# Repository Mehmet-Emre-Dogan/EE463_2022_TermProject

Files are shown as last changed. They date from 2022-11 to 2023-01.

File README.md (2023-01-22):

# EE463 2022 Term Project
2 kW Smart DC motor drive.
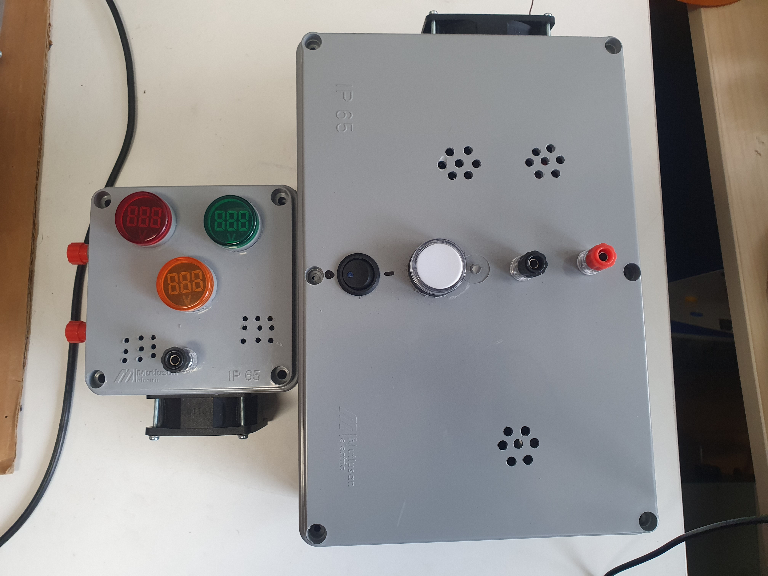
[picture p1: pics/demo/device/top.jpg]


# Circuit Diagrams

## Main Block Diagram
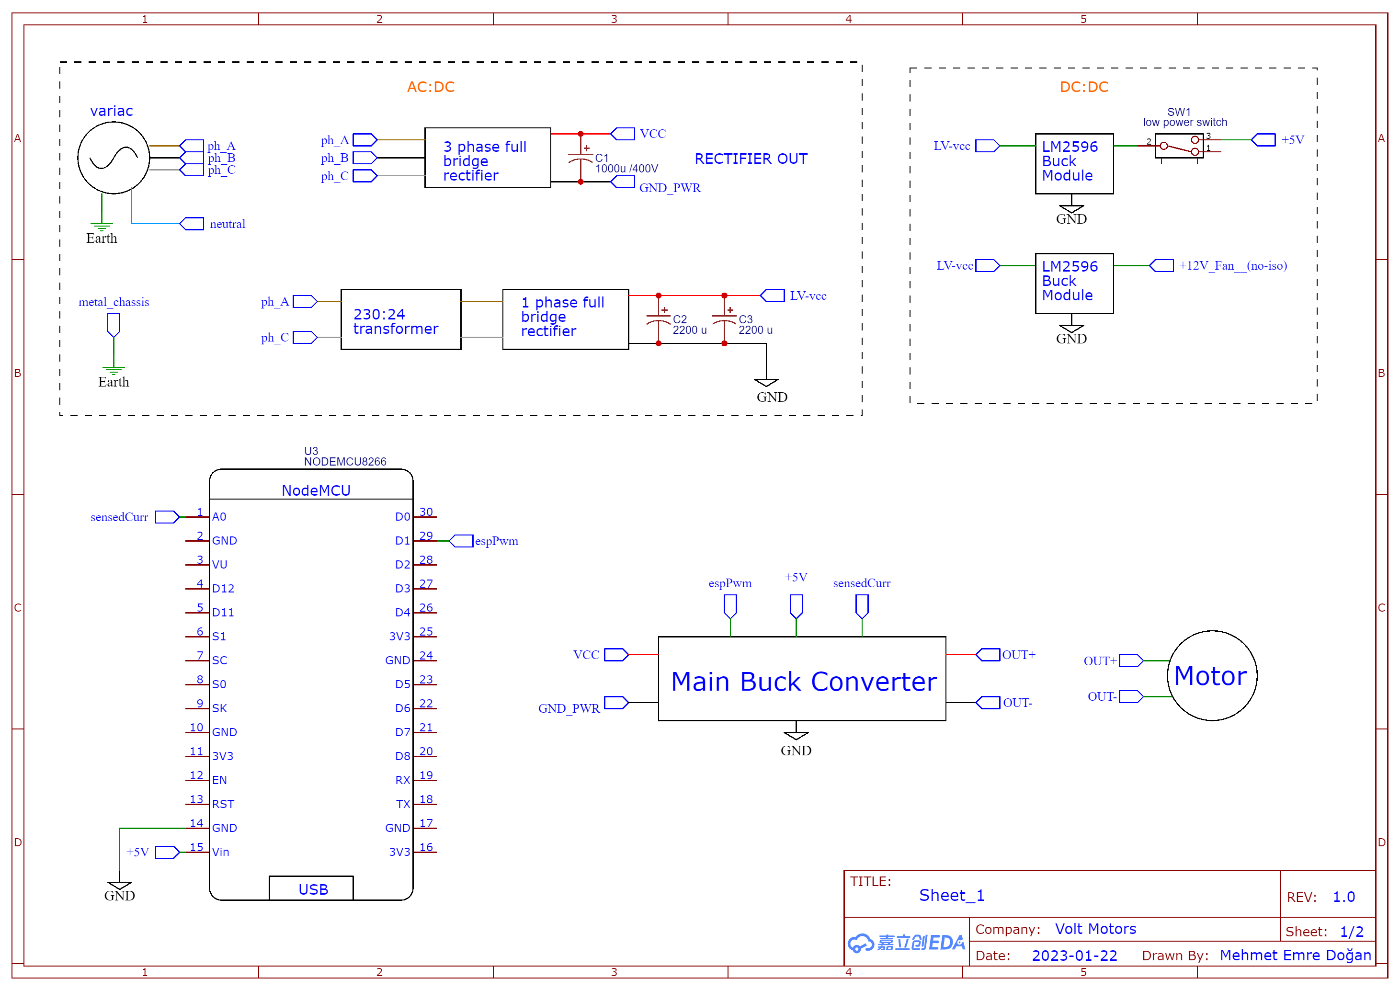
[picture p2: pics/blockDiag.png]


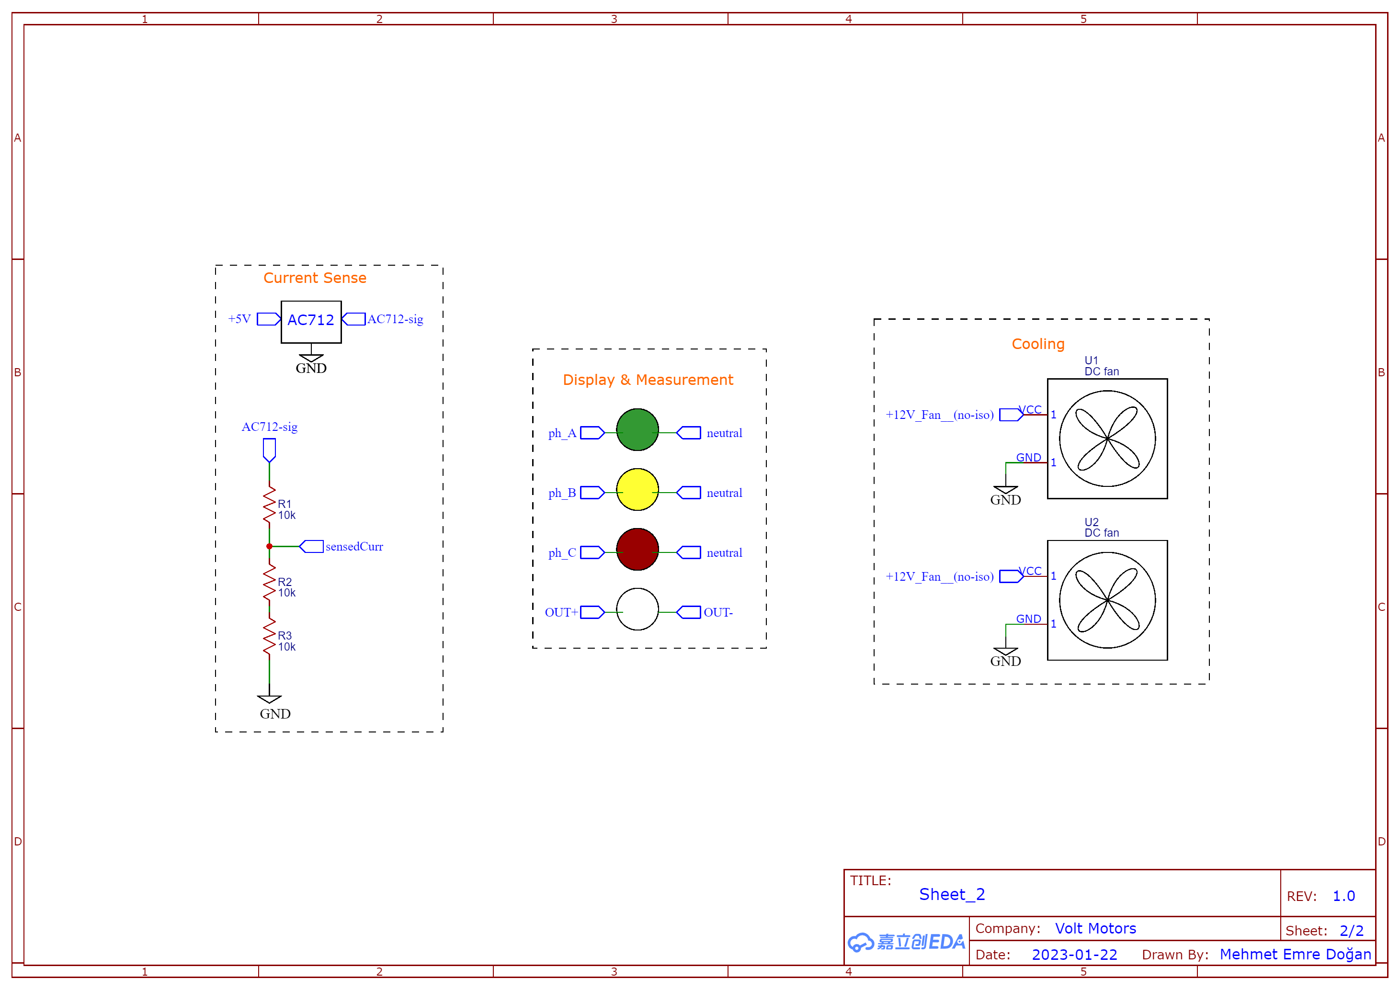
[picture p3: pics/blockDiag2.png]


## Main Buck Converter
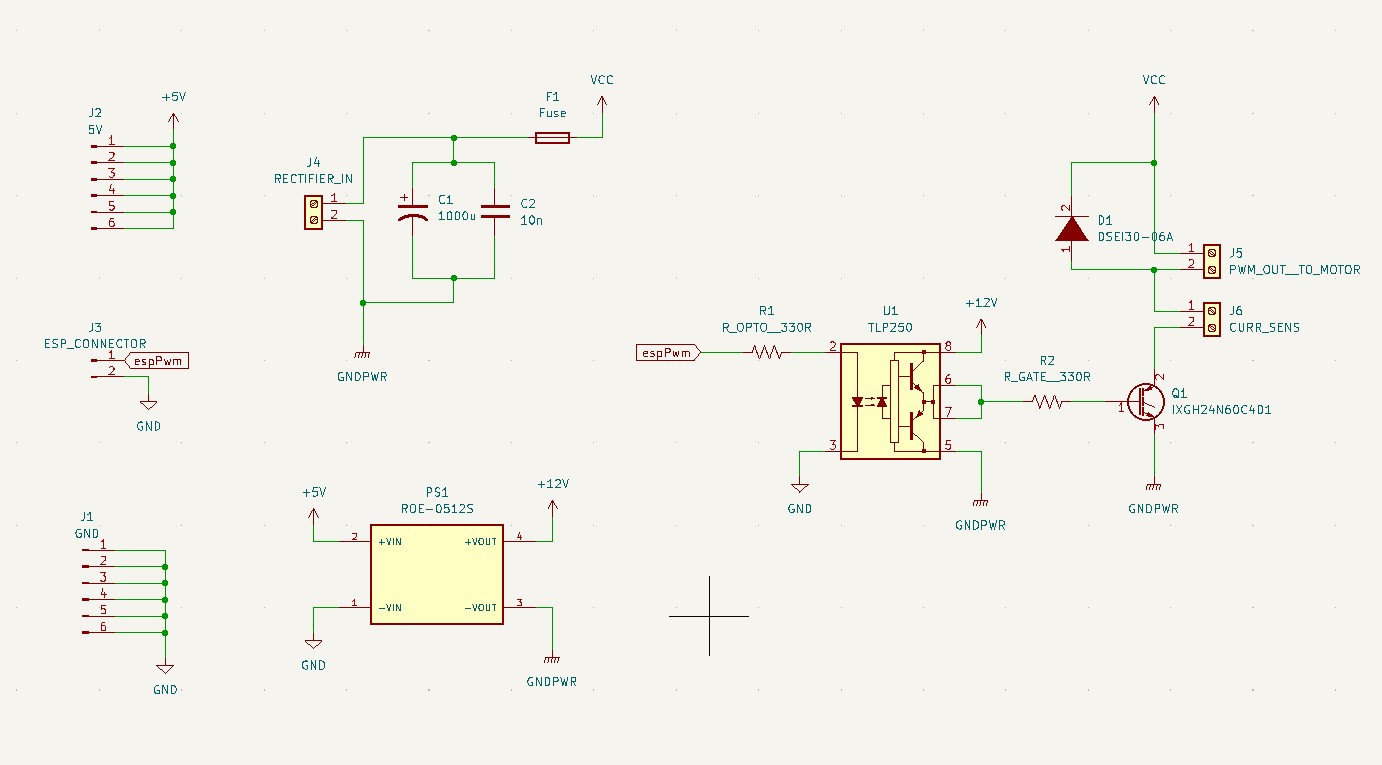
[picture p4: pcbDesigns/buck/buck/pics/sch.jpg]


## Low Power Adapter
### Schematic
<div align="center"> 

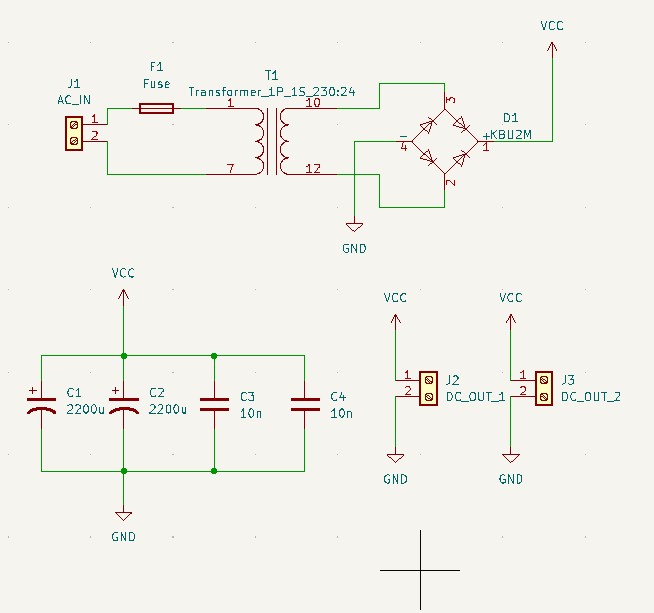
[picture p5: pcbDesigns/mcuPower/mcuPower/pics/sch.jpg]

</div>

### PCB
<div align="center"> 

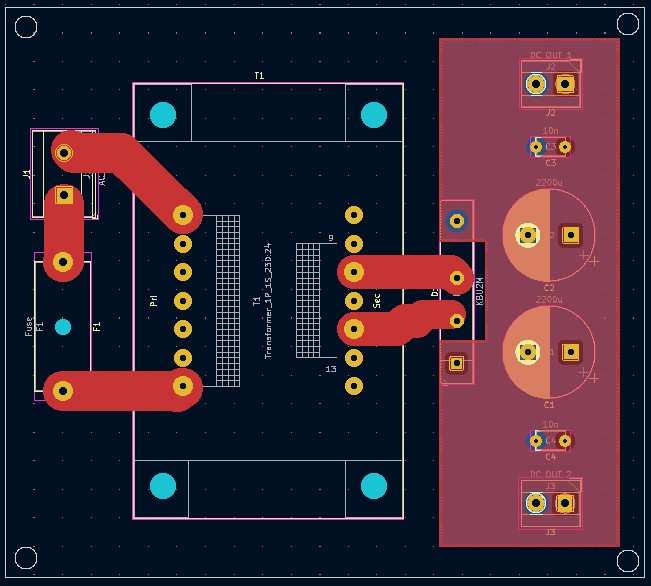
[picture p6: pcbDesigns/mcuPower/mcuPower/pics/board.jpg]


#### Top
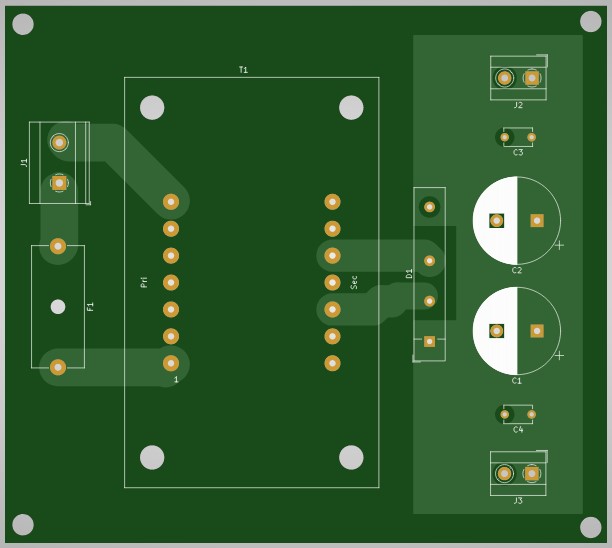
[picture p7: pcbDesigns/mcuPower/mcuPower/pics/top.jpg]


#### Bottom
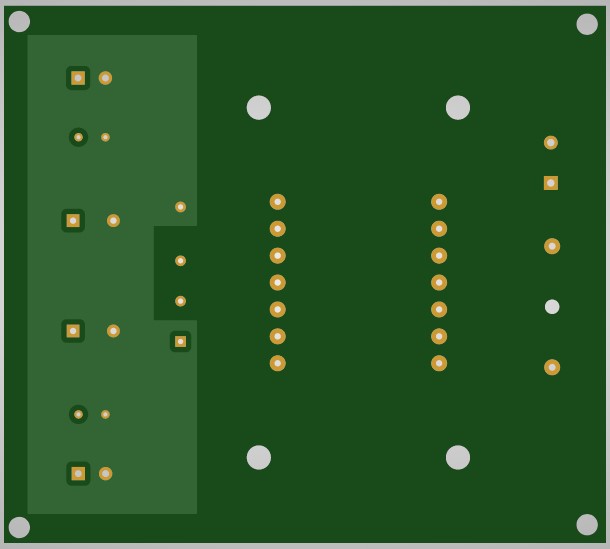
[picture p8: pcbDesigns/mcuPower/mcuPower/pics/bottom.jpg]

</div>

# Device
<div align="center"> 

## Top


## Side
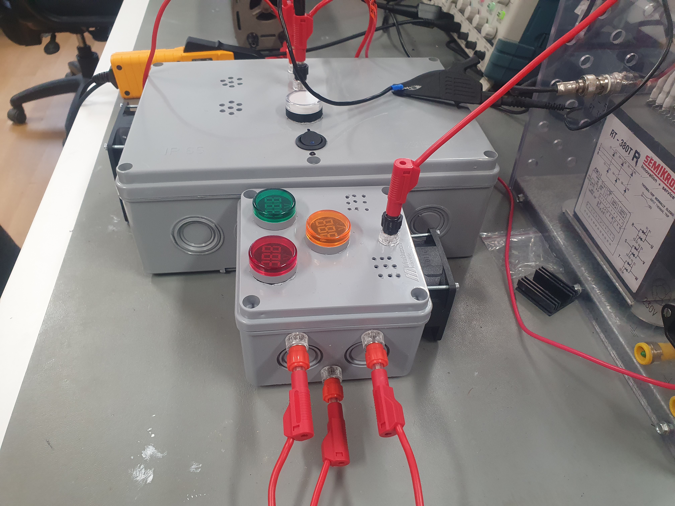
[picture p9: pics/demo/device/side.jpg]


## In
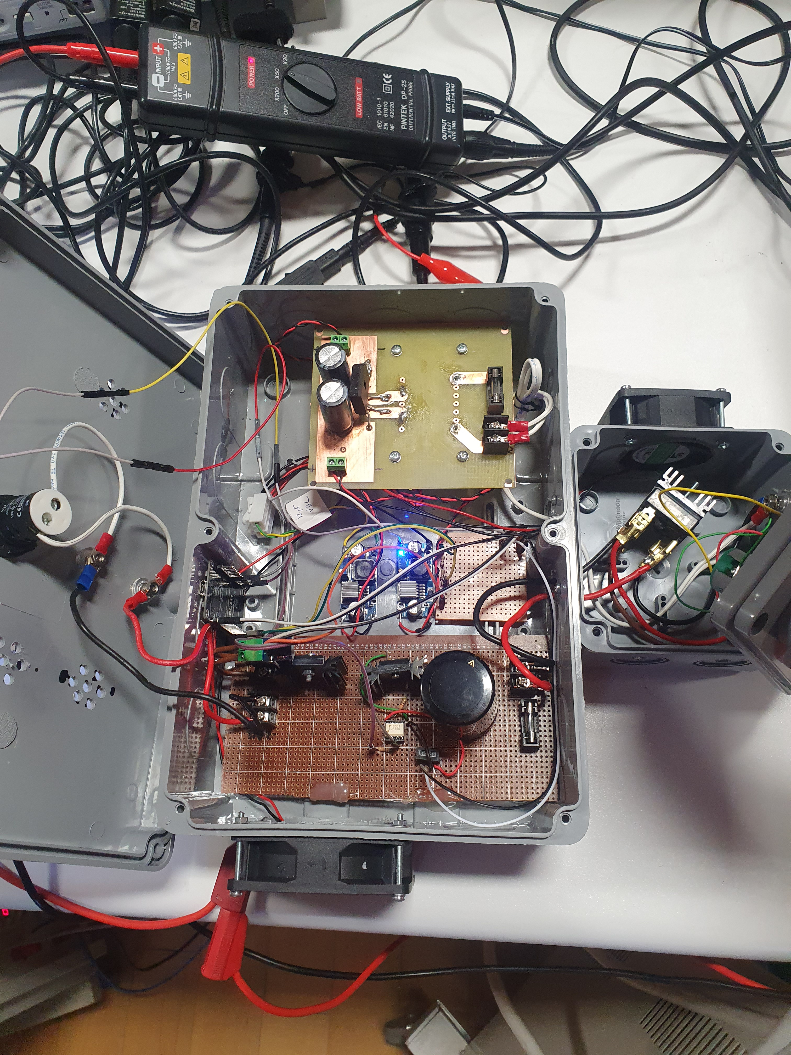
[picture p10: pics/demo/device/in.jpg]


## Line to Neutral
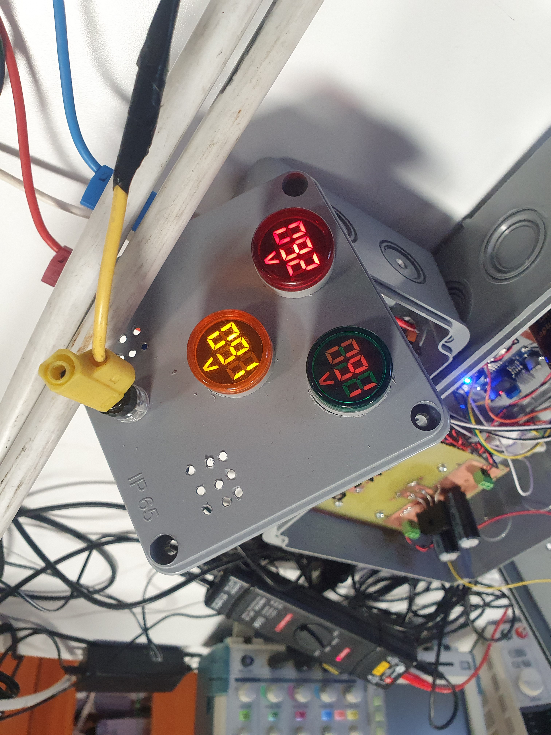
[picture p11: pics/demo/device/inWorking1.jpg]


## In [Wide Angle]
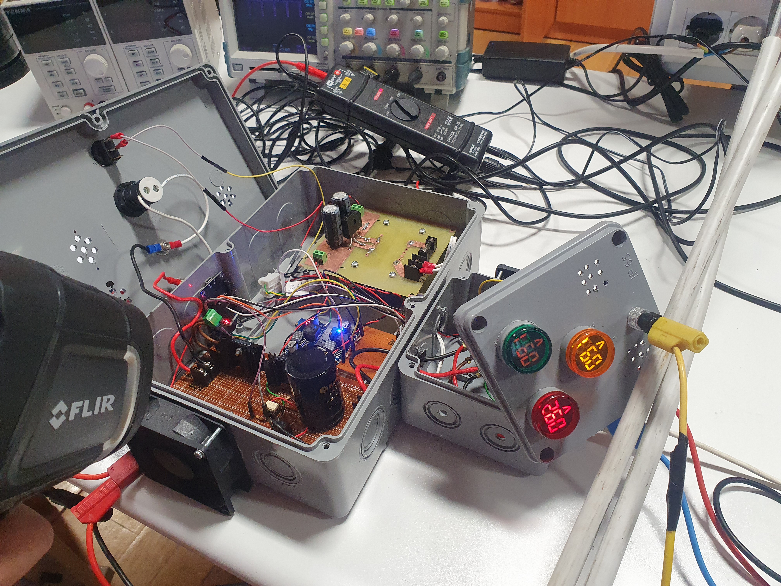
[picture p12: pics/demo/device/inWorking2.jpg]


</div>

# Analysis
## Power
### Rated Voltage [Loaded]
<div align="center">

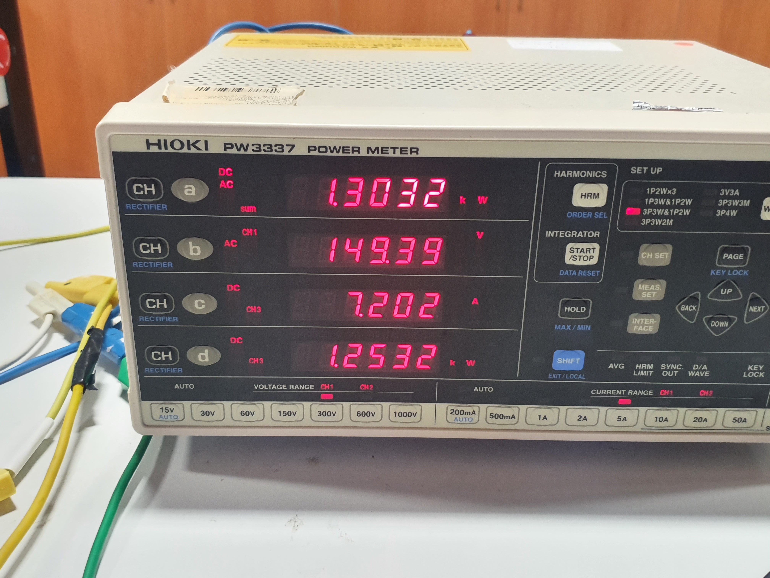
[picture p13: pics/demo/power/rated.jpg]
 </div>

### Rated Power [Loaded]
<div align="center">

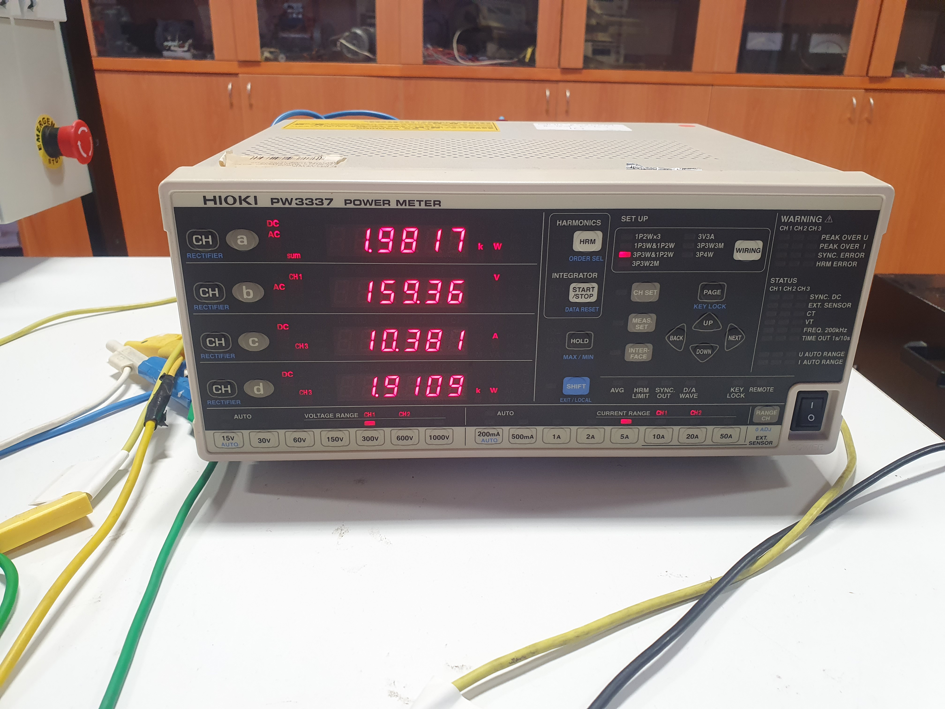
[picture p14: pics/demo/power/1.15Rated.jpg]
 </div>

## Waveforms

### Unloaded @v 25 % Duty
<div align="center">

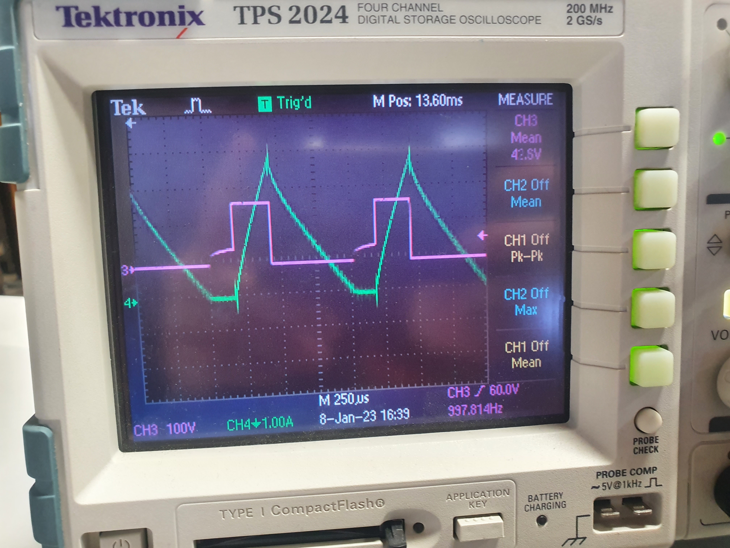
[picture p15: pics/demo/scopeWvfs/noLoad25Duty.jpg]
 </div>

## Thermals

### IGBT
<div align="center">

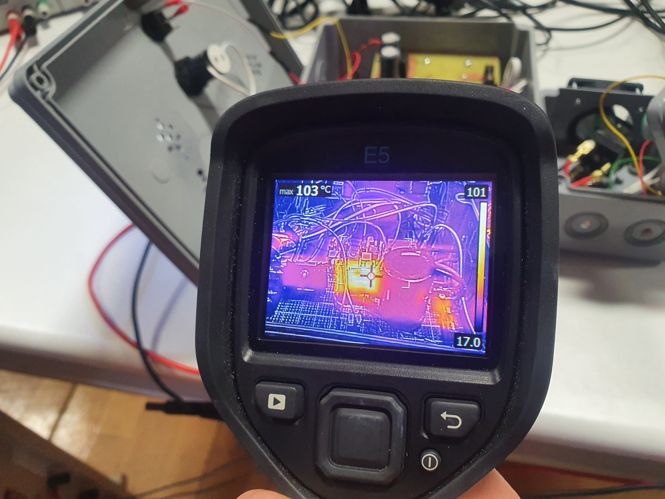
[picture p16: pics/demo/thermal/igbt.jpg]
 </div>

### 3 Phase Diode Rectifier

<div align="center">

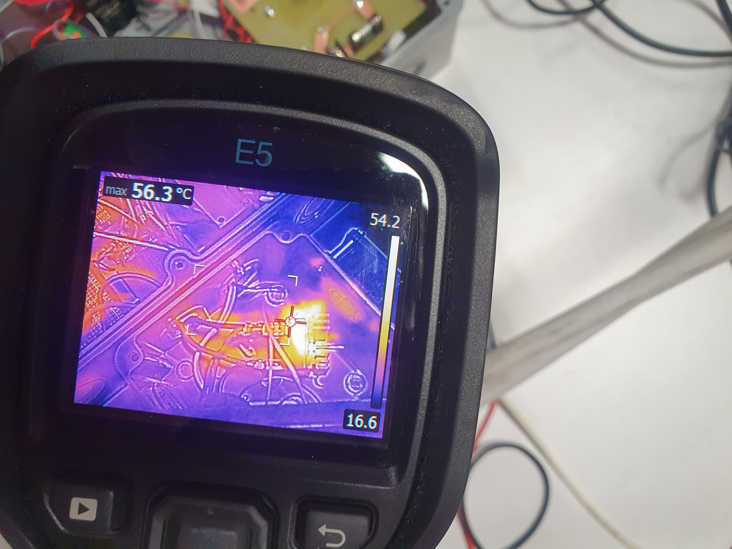
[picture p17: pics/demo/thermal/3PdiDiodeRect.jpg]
</div>

# Miscellaneous Demos
 ## Webserver Demo
 Webdemo could be seen via following the link below:

  https://medogan.com/test_server_demo/463_esp_webdemo.html
## IP Scanning
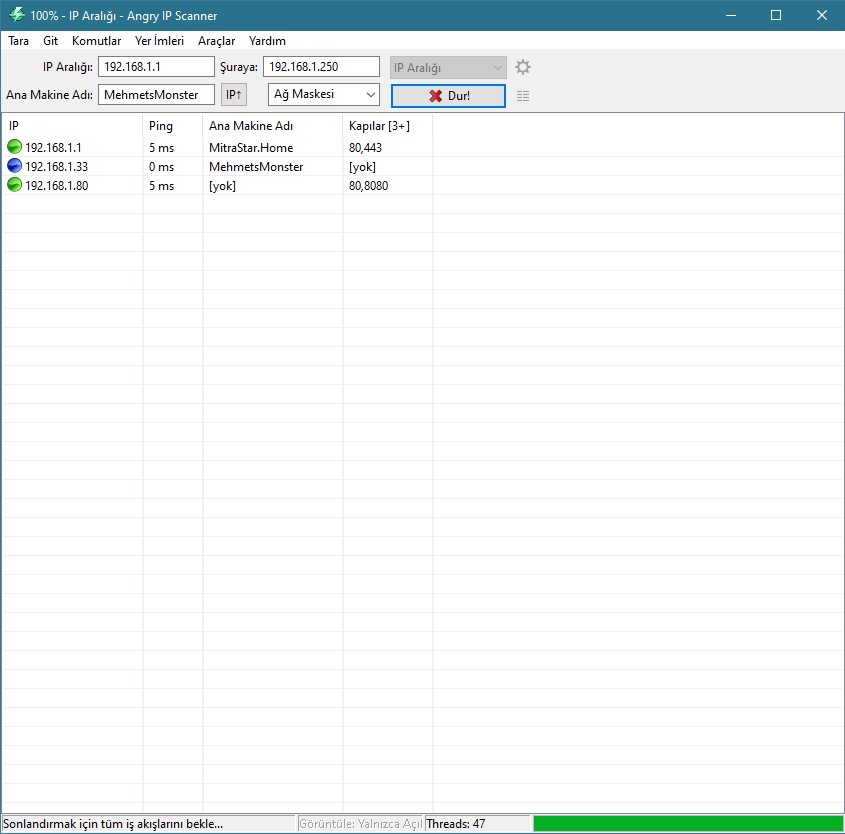
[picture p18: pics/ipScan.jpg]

## Controller
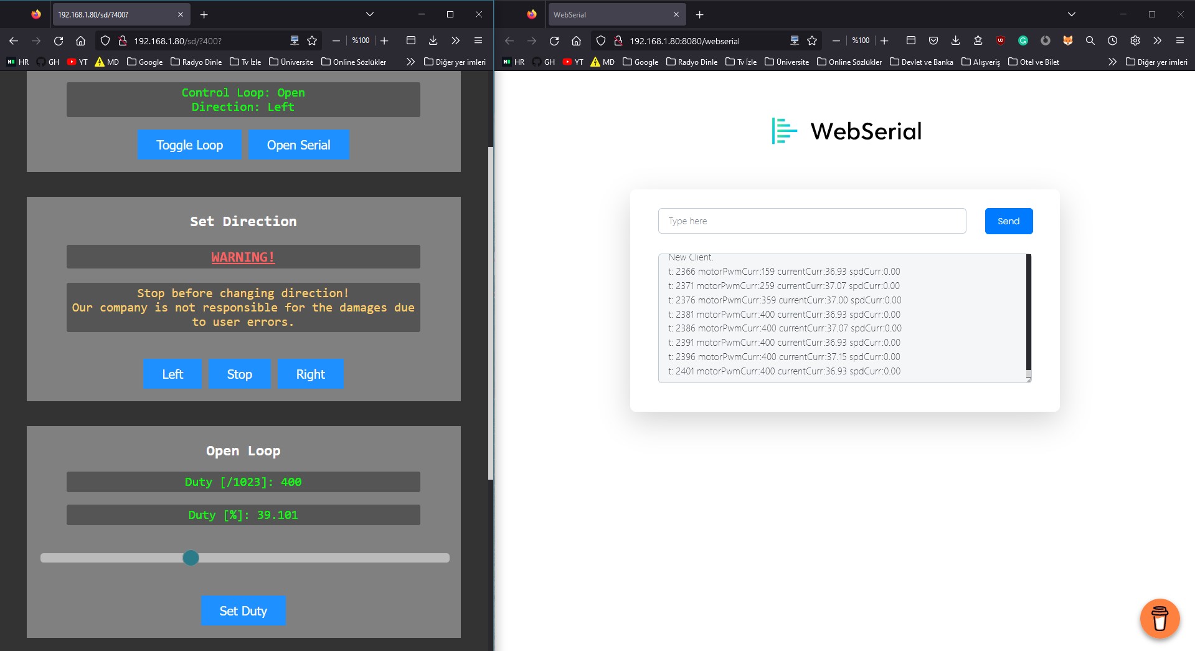
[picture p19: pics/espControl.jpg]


# Demo Videos

 ## Motor Lab Demo
 https://www.youtube.com/watch?v=8uU4kF-YDas

 ## Motor Lab Demo [ WebGui]
 https://www.youtube.com/watch?v=bq63kfShjrk

 ## ESP Soft Starting Demo
 https://www.youtube.com/watch?v=6NDupYknA6s

 ## Optocoupler Demo
https://www.youtube.com/watch?v=Q2luOk-gndQ

 ## Testing IRFP460 N Channel MOSFET
  https://www.youtube.com/watch?v=HJyMbZKjLFo
  
 IRFP460 was not used in the project because it is not supplied by the University and its is expensive and we've left only one. [We had 2 but we burned one of them.]
 IXGH24N60C4D1 N Channel IGBT was used due to it is supplied by the University .

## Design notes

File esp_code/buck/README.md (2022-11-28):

# ESP8266 Code

## Wireless Control Over Webpage
- [Online Test Demo](https://medogan.com/test_server_demo/463_esp_webdemo.html) [disclaimer: ESP is not connected to WAN, this link is just for demo]

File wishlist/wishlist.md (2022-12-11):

# Wishlist

## Bridge Rectifiers
- 36MT160 

## Diodes
- https://www.ozdisan.com/guc-yari-iletkenleri/diyot-modul-diyot-dogrultucular/hizli-diyotlar/DSEI30-06A --> 7 [4 for H bridge, 1 for dynamic braking, 2 redundancy]

## Mosfets
- https://www.ozdisan.com/guc-yari-iletkenleri/mosfetler/mosfet-discrete/LSIC1MO120E0080 --> 7 [4 for H bridge, 1 for dynamic braking, 2 for redundancy]

## Capacitors
- https://www.ozdisan.com/pasif-komponentler/kondansatorler/aluminyum-kondansatorler/K754001020PM0E050/503387 --> 3 [2 in parallels, 1 redundancy]

- https://www.ozdisan.com/pasif-komponentler/kondansatorler/aluminyum-kondansatorler/PKR1-063V222MJ350/337141 --> 10 [we need 4 but its cheap, lets buy more]

## Current Sensors
- https://www.direnc.net/acs714-akim-sensoru-30a30a-pololu --> 2 [to measure armature current, 1 redundancy]

## Heatsinks
- https://www.ozdisan.com/elektromekanik-komponentler/sogutucular/aluminyum-sogutucular/ZHS-45ASD35MM/354769 --> 11 [8 for H bridge, 2 for dynamic braking, 1 redundancy]

## Transformers
- https://www.ozdisan.com/pasif-komponentler/trafolar/genel-tip-trafolar/ASL171124/508554 --> 2 [1 for fans, 1 for others]

## Fans
- https://www.ozdisan.com/elektromekanik-komponentler/fanlar/genel-tip-fanlar/DA08025S12L/443558 --> 2
- https://www.ozdisan.com/elektromekanik-komponentler/fanlar/fan-aksesuarlari/PF-08/399241 --> 2
- https://www.ozdisan.com/elektromekanik-komponentler/fanlar/fan-aksesuarlari/MG-08/399249 --> 2

## Converters
- https://www.ozdisan.com/maker-ve-iot-urunleri/arduino/arduino-modulleri/LM2596-DC-DC-STEP-DOWN/591638 --> 3 [1 for MCU, 1 for fans, 1 for rest of the control CCT]

## Connectors
- https://www.motorobit.com/urun/2-pin-bariyer-klemens-7-62mm-kf25c-7-62 --> 8 [rectified DC in, controller AC in, motor out, brake out, 4 redundancy]
- In case kf25c fails:  https://ozdisan.com/konnektor-ve-baglanti-elemanlari/klemensler/pcb-klemensler/DG636-7-62-02P-14-00AH/358216 --> 8 [rectified DC in, controller AC in, motor out, brake out, 4 redundancy]

- https://www.robotistan.com/1x40-180-disi --> 3 
- https://www.robotistan.com/1x40-180-15mm --> 3

## Screws
- Metric 4x40 mm --> 12 [to mount fans, 4 redundancy]
- Metric 3x10 mm --> 20 [to mount heatsinhs, 10 redundancy]

## Nuts
- Metric 4 mm --> 12
- Metric 3 mm --> 20

## Sockets
- https://www.robotistan.com/8-pin-dip-socket [for optos and opamps]
- https://www.robotistan.com/14-pin-dip-soket [for optos and opamps]

## MCU
- https://www.robotistan.com/nodemcu-lolin-esp8266-gelistirme-karti-usb-chip-ch340 --> 1

## ADC
- https://www.robotistan.com/ads1115-16-bit-4-kanal-adc --> 1

## Temperature Sensor
- https://www.robotistan.com/lm35 --> 3 [1, 1 to compare measurements, 1 redundancy]

## Low Power Mosfet
- https://www.motorobit.com/urun/irf3205-55v-110a-mosfet-to220 --> 2 [ to drive fans]

## Screen
- https://www.robotistan.com/096-inch-i2c-oled-ekran-ssd1306 --> 1 [for menu display] 

## Rotary Encoder
- https://www.robotistan.com/rotary-enkoder-arduino-uyumlu --> 2 [for menu display] 

## Various Sensors
- https://www.robotistan.com/infrared-mesafe-sensoru-220cm --> 2 [1 for rpm feedback, 1 redundancy]

## Switch & Pot
- For menu control
- https://www.robotistan.com/ic118-mini-isikli-anahtar --> 2 
- https://www.robotistan.com/10k-potansiyometre-ayarli-direnc --> 1 
- https://www.robotistan.com/10kohm-dogrusal-potansiyometre --> 1
- https://www.robotistan.com/kn113-potansiyometre-basligi-kirmizi --> 2 [for rotaries and pots]

- https://www.robotistan.com/10k-cok-turlu-trimpot-dik-3296w-1-103 --> 5 [ for opamps]

## MUX
- https://www.robotistan.com/cd74hc4067-16-kanal-analog-dijital-multiplexer --> [we need more outputs]

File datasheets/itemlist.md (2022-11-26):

# Itemlist

## 3 Phi Full Bridge Diode Rectifiers
- [x] [SQL50A 50A 1200V Alüminyum 3 Fazlı Köprü Diyot](https://www.motorobit.com/urun/sql50a-50a-1200v-aluminyum-3-fazli-kopru-diyot)
- [x] [SKBPC5010 50A 1000V Trifaze Köprü Diyot 3 Faz](https://www.motorobit.com/urun/skbpc5010-50a-1000v-trifaze-kopru-diyot-3-faz)

## MCU
- [x] [NodeMCU LoLin ESP8266 Geliştirme Kartı - USB Chip](https://www.motorobit.com/urun/nodemcu-lolin-esp8266-gelistirme-karti-usb-chip)

## MOSFETs & IGBTs
- [x] [IRFP460 - 500V 20A Mosfet - TO247](https://www.motorobit.com/urun/irfp460-500v-20a-mosfet-to247)
- [x] [IRFP250N - 200V 30A Mosfet - TO247](https://www.motorobit.com/urun/irfp250n-200v-30a-mosfet-to247)
- [x] [IRFP254 - 250V 23A Mosfet - TO247](https://www.motorobit.com/urun/irfp254-250v-23a-mosfet-to247)

<br>

- [x] [SGH40N60 - G40N60 600V 40A IGBT Mosfet - TO247](https://www.motorobit.com/urun/sgh40n60-600v-40a-igbt-mosfet-to247)

## Heatsinks
- [x] [TO220 Alüminyum Soğutucu Heatsink 15x10x20mm](https://www.motorobit.com/urun/to220-aluminyum-sogutucu-heatsink-15x10x20mm)
- [x] [TO247 Metal Soğutucu Heatsink 25x34x12mm](https://www.motorobit.com/urun/to247-metal-sogutucu-heatsink-25x34x12mm)
- [x] [Alüminyum Soğutucu 50x25x10mm](https://www.motorobit.com/urun/aluminyum-sogutucu-50x25x10mm)

## Connectors

- [x] [KF301V 5.0-2P](https://www.robotistan.com/kf301v-5)
- [x] [3 Pinli Klemens](https://www.motorobit.com/urun/3-pinli-klemens)
- [x] [2 Pinli Klemens](https://www.motorobit.com/urun/2-pinli-klemens)
- [x] [No2 Sıra Klemens (Mavi)](https://www.hepsiburada.com/mutlusan-no2-sira-klemens-mavi-p-HBV0000060C0M?magaza=ÖZ%20EMEK%20ELEKTRİK)

## Copper Dot
- [x] [8x12cm Epoxy Çift Taraflı Delikli Plaket](https://www.motorobit.com/urun/8x12cm-epoxy-cift-tarafli-delikli-plaket)
- [x] [13x25cm Delikli Plaket](https://www.motorobit.com/urun/13x25cm-delikli-plaket)

## Accessories
- [x] [Çetsan Kablo Bağı Cırt Kelepçe](https://www.hepsiburada.com/cetsan-kablo-bagi-cirt-kelepce-siyah-2-5-x-200-mm-100-lu-p-HBV00000VG20V?magaza=ÖZ%20EMEK%20ELEKTRİK)

## Feedback Equipment
- [ ]

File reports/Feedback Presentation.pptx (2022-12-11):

## EE463 Static Power Conversion Hardware Project Feedback Presentation

- Ömer Şen
- Gamze Çelik
- Mehmet Emre Doğan

## Outline

- Problem Definition
- Topology Selection
- Simulation Result
- Targeted Bonuses
- Calculations
- Component Selection
- Thermal Calculation
- Conclusion

## Problem Definition

- Power Input: 3 Phase, or 1 Phase AC Grid (Adjustable with variac)
- Output: Adjustable DC Output (Vout,max = 180 V)

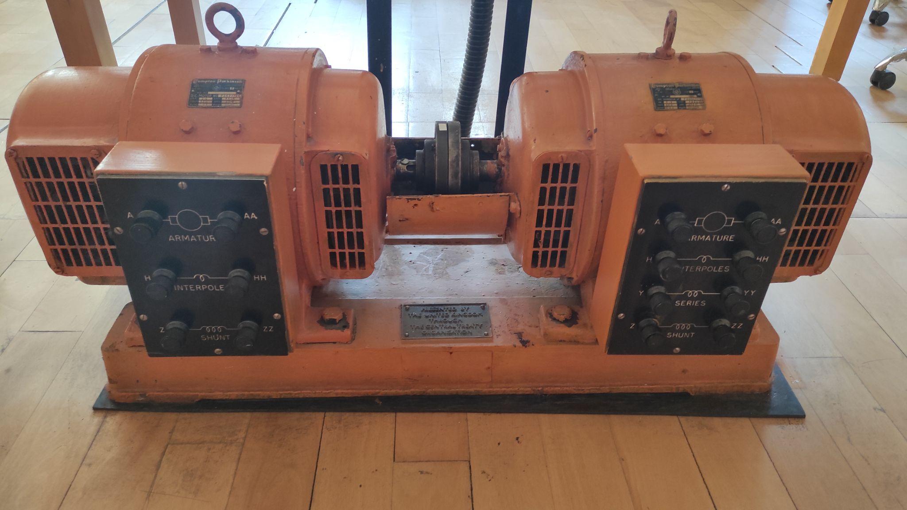
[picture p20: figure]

## Topology Selection

- Three Phase Thyristor Rectifier
- Single Phase Thyristor Rectifier
- Diode Rectifier + Buck Converter

- Low Ripple - Expensive
- High Voltage - Synchronization
- No Third Harmonics - 6 Gate Signal

- High Ripple + Low Cost
- Low output Voltage

- Low Ripple + More Efficient
- High Voltage + Easy Speed Control
- No Third Harmonics

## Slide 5

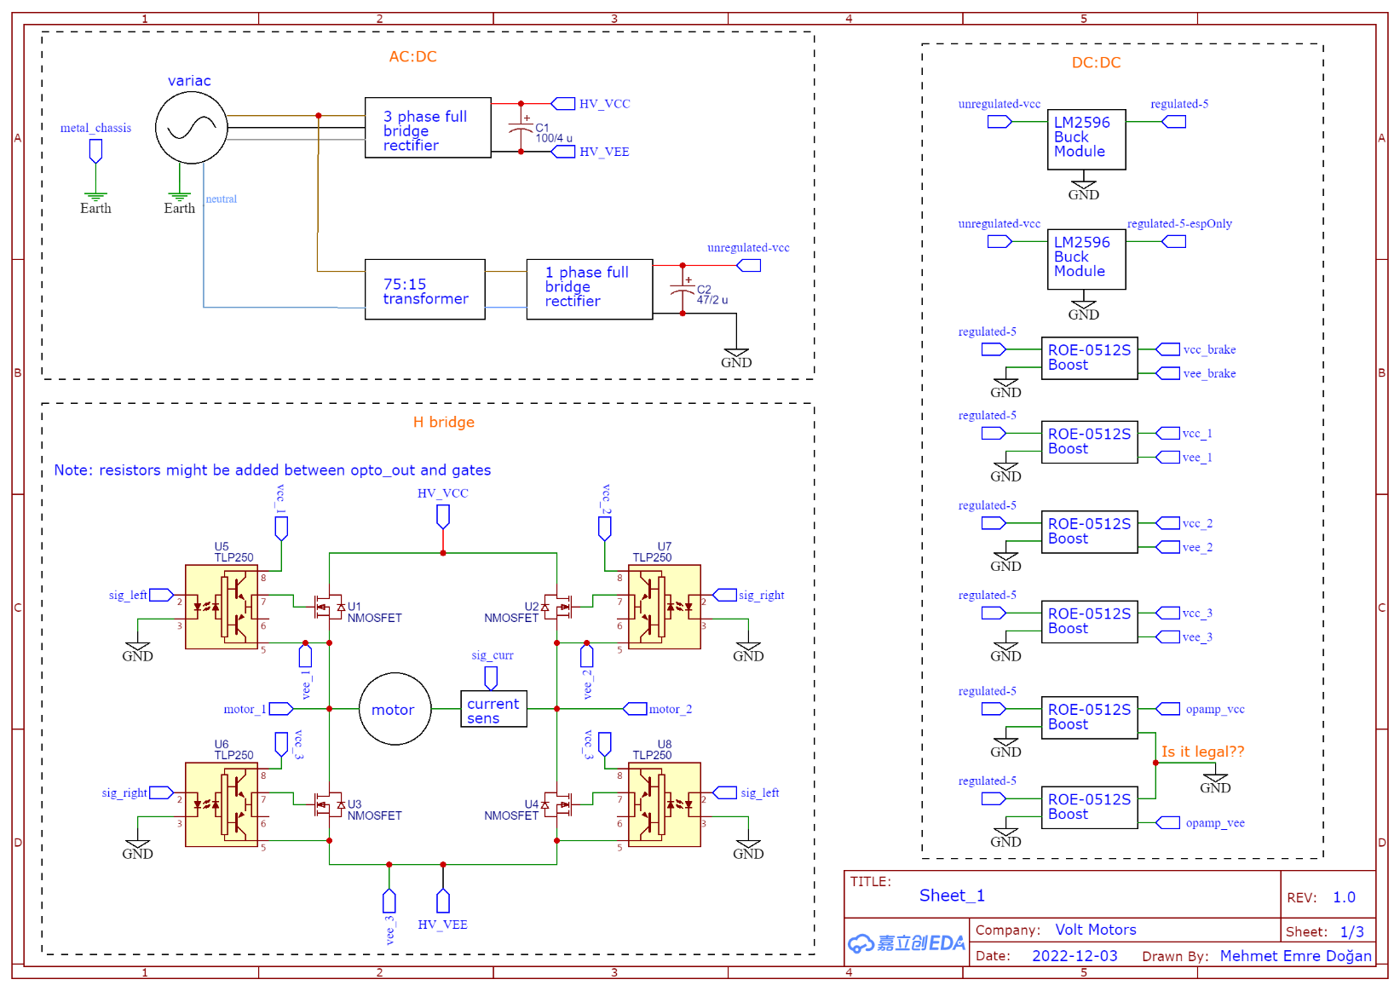
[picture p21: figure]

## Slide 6

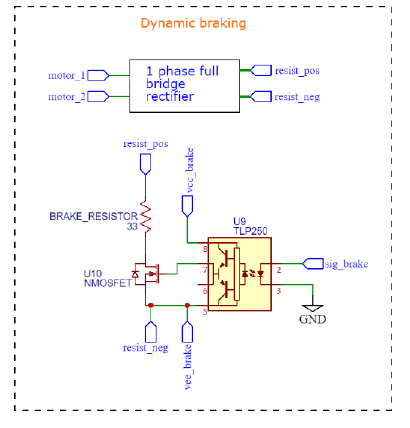
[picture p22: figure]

Resistor is externally connected via banana plugs

## Simulation Result

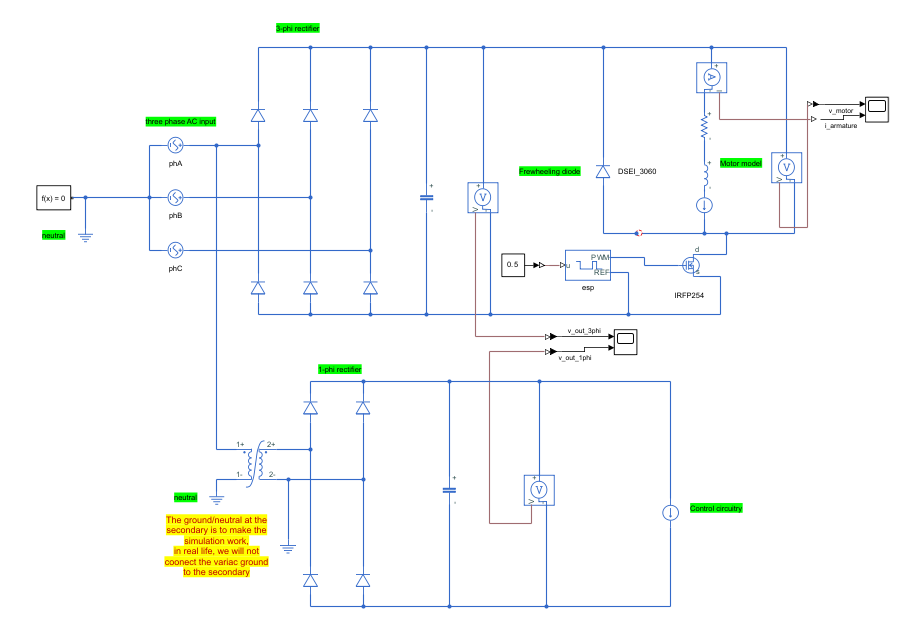
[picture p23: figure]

Simulation Circuitry

## Simulation Result

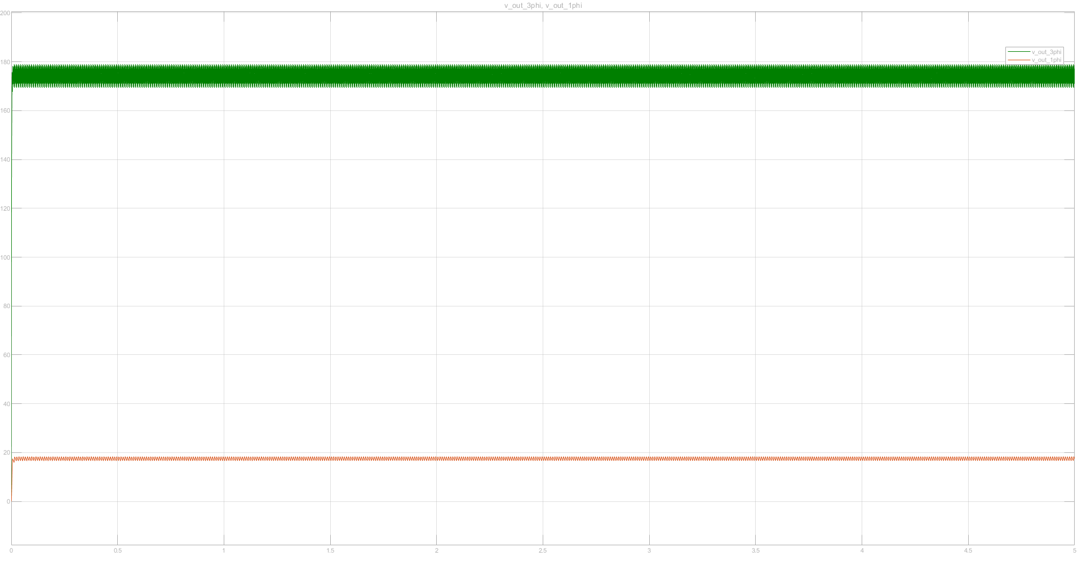
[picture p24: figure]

Stability Simulation of Rectifiers

## Simulation Result

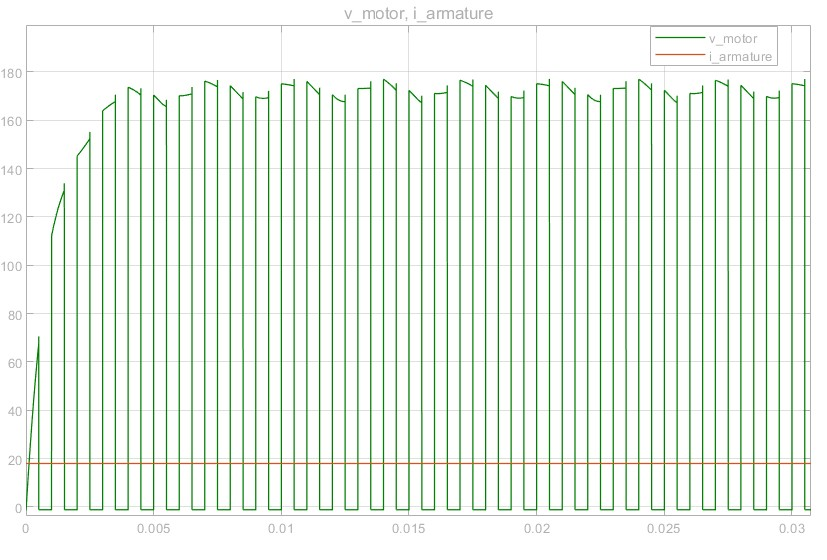
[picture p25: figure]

Terminal Rating of DC Motor After PWM Signal

## Targeted Bonuses

- Tea Bonus
- PCB Bonus
- Efficiency Bonus
- Industrial Design Bonus
- Single Supply Bonus
- Closed-Loop Voltage/Current Control Bonus
- Closed-Loop Speed Control Bonus
- Four-Quadrant Bonus

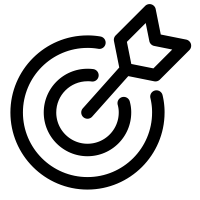
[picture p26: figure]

## Calculations

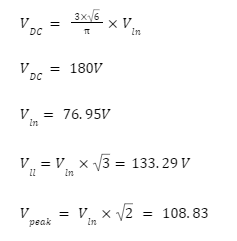
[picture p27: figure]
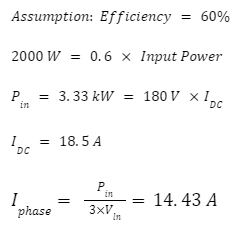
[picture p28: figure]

## Component Selection

Bridge Rectifier | 36MT160 | 1600V | 35A
MOSFET | LSIC1MO120E0080 | 1200V | 39A (25 °C)
Diode | DSEI30-06A | 600V | 37A
Capacitor | K754001020PM0E050 | 400V | 1000uF
Current Sensor | ACS714 | ∓30A
Infrared Distance Sensor

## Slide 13

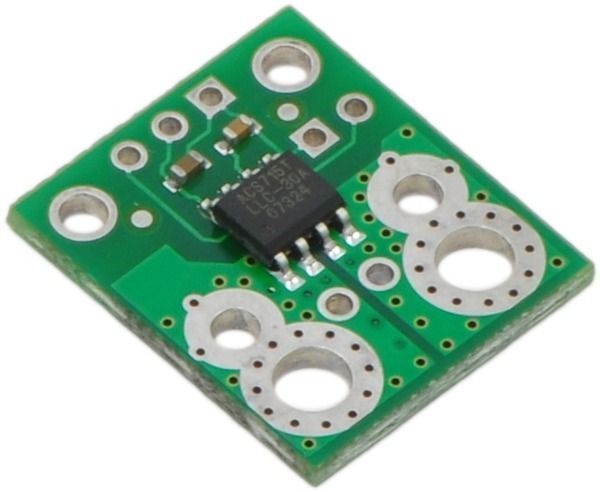
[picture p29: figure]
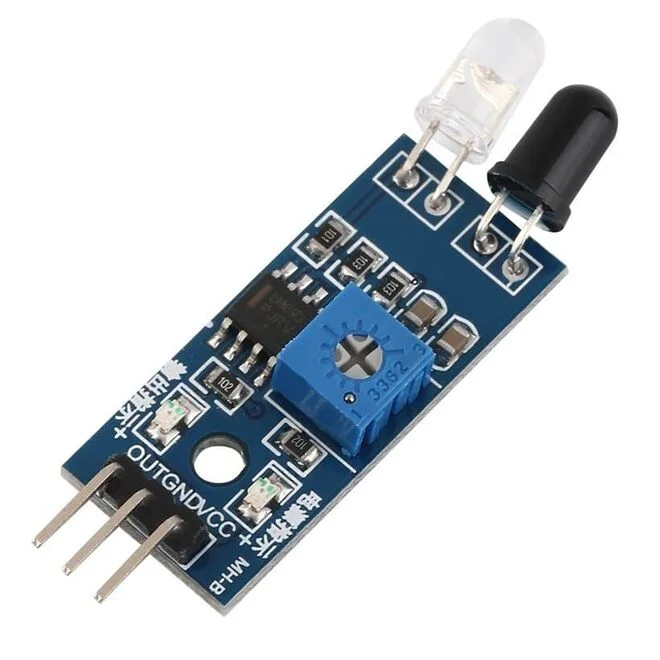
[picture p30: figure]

Infrared Distance Sensor

Current Sensor

## Thermal Calculations

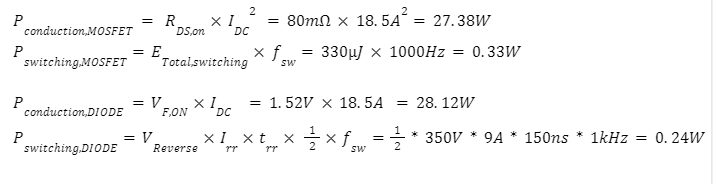
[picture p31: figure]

## Conclusion

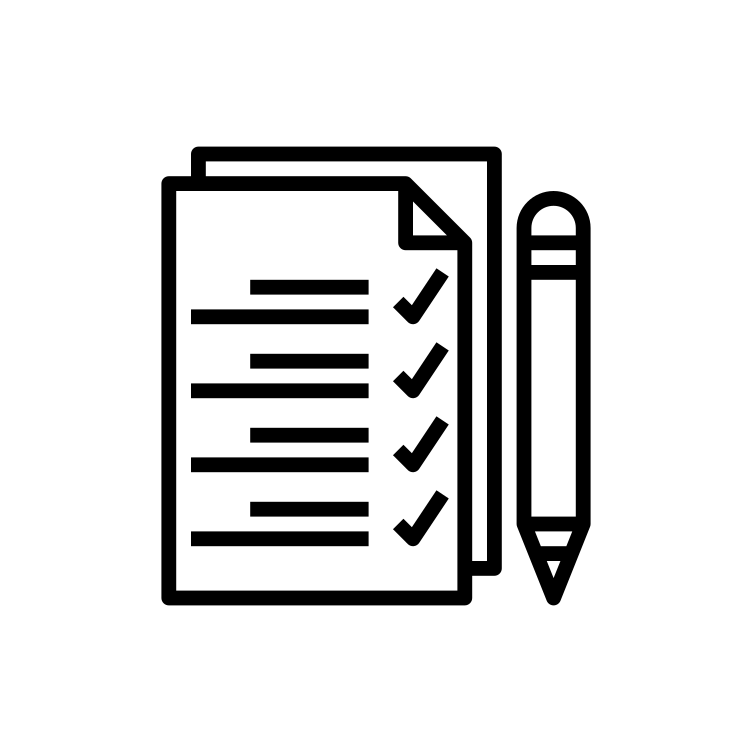
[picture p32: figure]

Tests

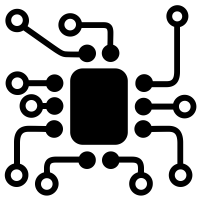
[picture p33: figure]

PCB Design

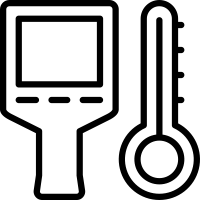
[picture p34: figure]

Thermal Analysis

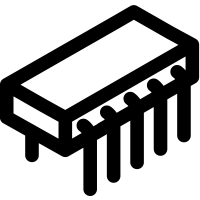
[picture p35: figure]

Implementation

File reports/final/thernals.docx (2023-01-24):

P_(loss,conduction, IGBT) =V_(CE, sat) ∙I_(avg) ∙Duty≅ 1.9V∙10.4A∙0.9=17.784W

P_(loss,switching, IGBT) =E_(switching,total) ∙f_(switching) ≅ 1.46mJ∙1kHz=1.46 W

P_(loss,total, IGBT) =19.244W

P_(loss,conduction,diode) =V_(fwd) ∙I_(avg) ∙(1-Duty)≅ 1.52V∙10.4A∙0.1=1.58W

P_(loss,switching,diode) =(1/2∙C_R ∙V_R ^2 +1/6∙I_(RR) ∙V_R ∙t_b )∙f_(switching)

≅ (1/2∙2pF∙600V^2 +1/6∙9A∙600V∙150ns/2)∙1kHz=0.068 W

P_(loss,total, diode) =1.648W

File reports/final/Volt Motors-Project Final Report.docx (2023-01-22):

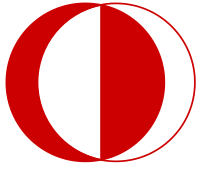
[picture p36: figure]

# EE463 Static Power Conversion I

# Term Project Final Report

## Volt Motors

## Mehmet Emre DOĞAN – 2374825

## Gamze ÇELİK – 2304327

## Ömer ŞEN – 2305415

## Introduction

In this project, a DC Motor Drive will be designed and implemented. The drive will run a DC motor when it is supplied by an AC source. In this report, aimed bonuses will be provided initially since the aims directs the topology. Then, Topology will be provided, and necessary simulation results will be given. Next, physical implementation work that has been done so far will be showed.

## Targeted Bonuses

### 1- Tea Bonus

One of the aimed bonuses it that providing 2kW for 5 minutes to boil a water and make an glass of hot tea.

### 2- PCB Bonus

An implementation of the system to a PCB is planned for not only the bonus points but also for building more robust system.

### 3- Efficiency Bonus

One of the goals is that constructing the most efficient circuit that fulfills the function. However, the bonus is not only depending on the circuit but also depends on the other groups circuits. Therefore, making the system as efficient as possible is the goal at that point.

### 4- Industrial Design Bonus

In order to protect the system from the outside impacts and crushes, it will be covered by a case.

### 5- Single Supply Bonus

The system is designed to supply only with a one AC source. Rest of the voltage level(s) will be obtained by inside converters.

### 6- Closed-Loop Voltage/Current Control Bonus

In order to protect the components from the high current, a closed feedback loop will be implemented by a current sensor.

### 7- Closed-Loop Speed Control Bonus

In order to obtain the speed of the motor and construct a speed control loop, an infrared sensor will be utilized.

### 8- Four-Quadrant Bonus

To operate in all the quadrants, 4 MOSFETs will be driven by 3 isolated drivers and OpAmp control.

## Topology


Figure 1: First Sheet of Topology

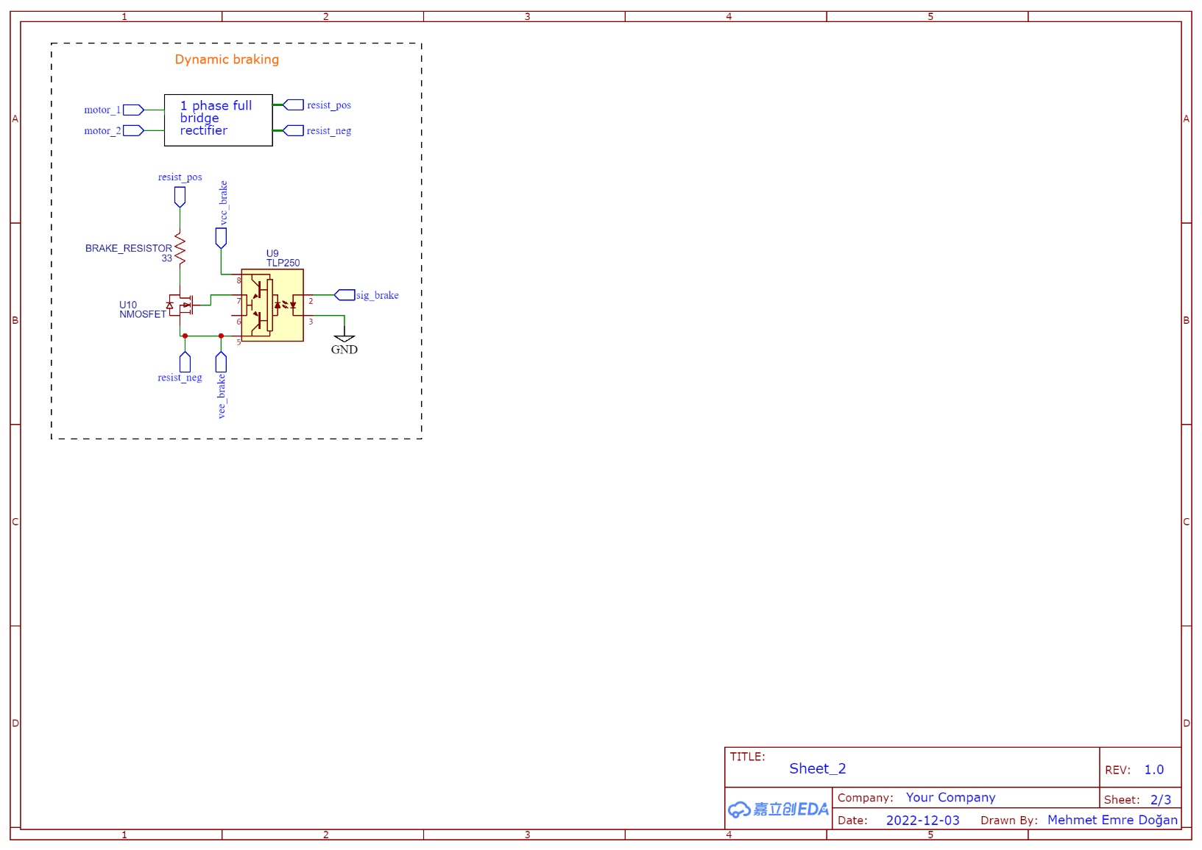
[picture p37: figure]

Figure 2: Second Sheet of Topology

Due to ease of usage of three phase full bridge rectifier + buck converter topology compared to other two topologies, three phase full bridge rectifier + buck converter is chosen as can be seen from the Figure 3. Moreover, the team is more experienced with the buck converter, which is another reason to choose buck converter topology. Also, implementing a topology which works in four of the quadrants, which is a determined feature by the team, would be very difficult by using thyristor. Therefore, H bridge topology is chosen to operate in four of the quadrants.

In order to supply the system with only one voltage source several converters are added to the topology, which can be seen from the Figure 1. Also, a transformer will be placed in the topology to provide required voltage level to the control circuitry. Output of the transformer will be rectified by a single-phase rectifier. After filtering, the closed loop buck converter which comes next will provide 5VDC output voltage.

Speed control feedback loop will be implemented by software that functions as PID. Input signal of the PID controller will be taken with infrared sensor.

Current control will be implemented by current sensor which will be connected in series to the armature terminals.

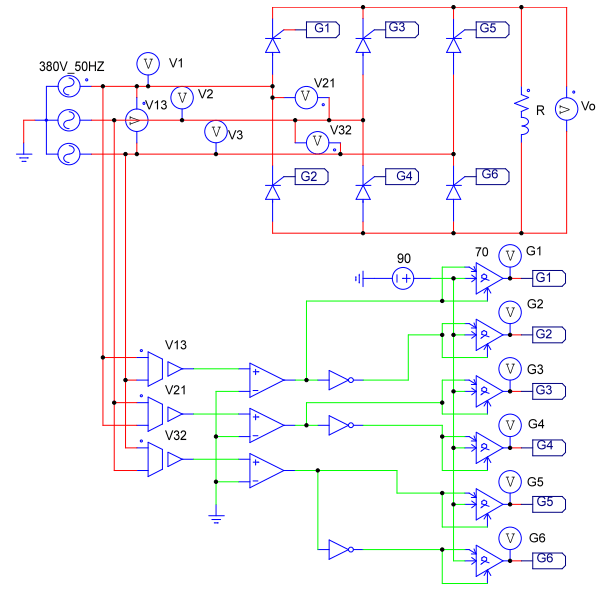
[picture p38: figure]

Figure 3: Thyristor Rectifier Circuit [1]

## Simulation Results


Figure 4: Simulation Circuitry

Basic purpose of the simulation is obtaining component ratings. The most important issue with the H bridge is determining the driving algorithm of the H bridge, which is hard to simulate in Simulink. As a result, H bridge is not implemented in Simulink.

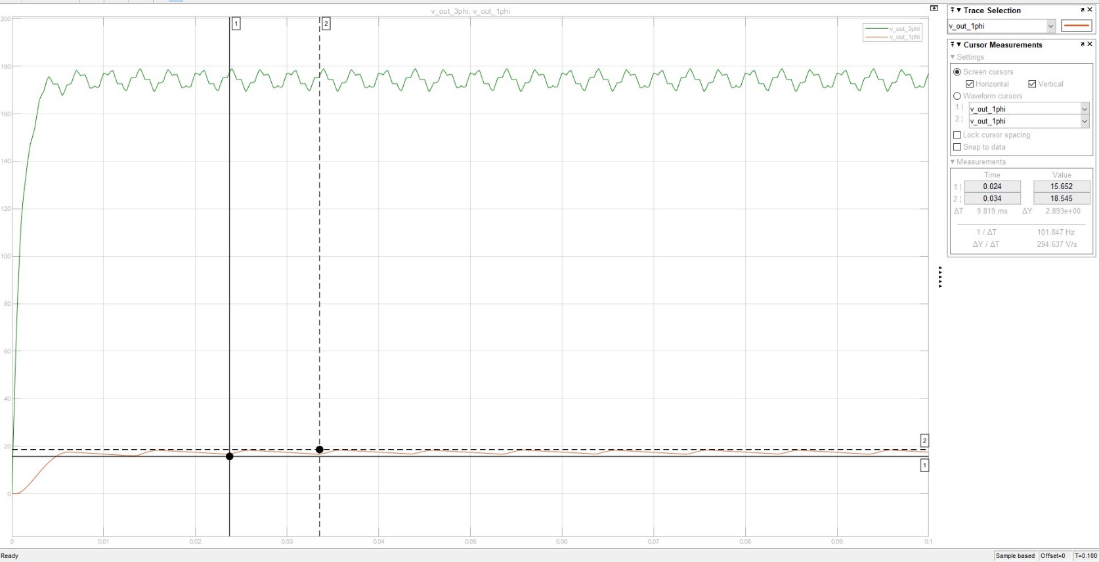
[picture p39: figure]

Figure 5: Control Circuitry Input Voltage

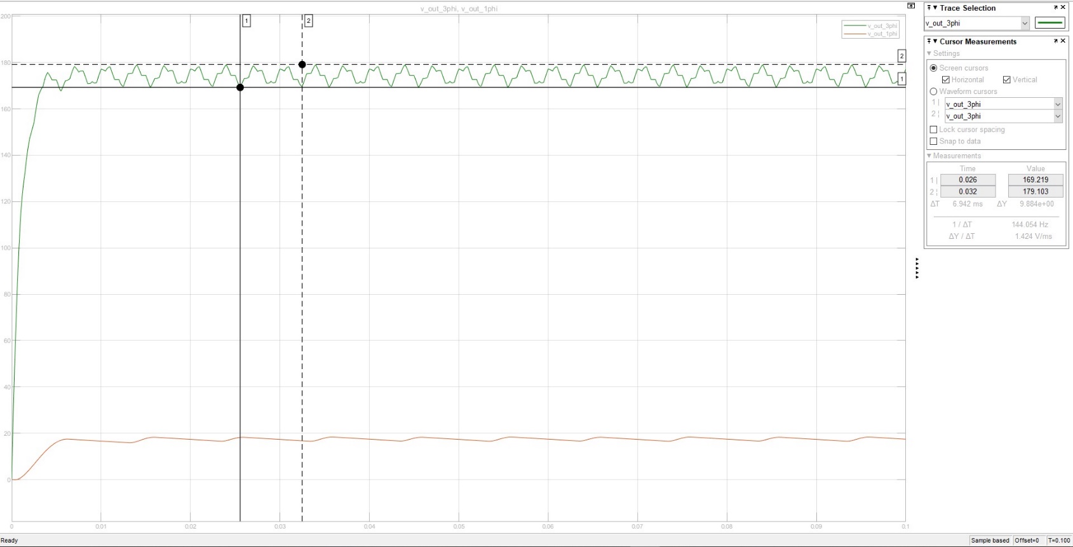
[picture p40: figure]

Figure 6: Motor Terminal Voltage Before PWM Signal


Figure 7: Stability Simulation of Rectifiers

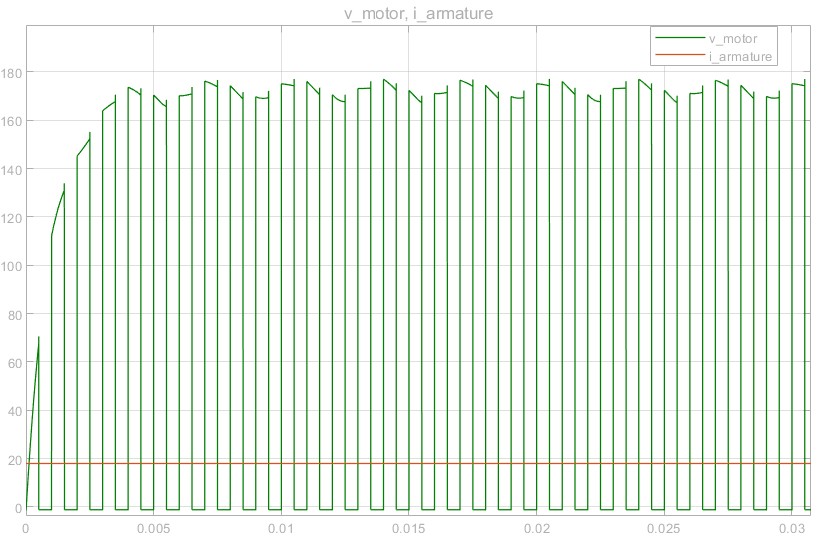
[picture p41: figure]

Figure 8: Terminal Rating of DC Motor After PWM Signal

## Component Selection

### Matlab Calculations

Base Calculation

clearvars

format shortEng

syms v_ln

vDc = (3*sqrt(6)/pi)*v_ln

vDc =

vDcWanted = 180

vDcWanted =

180.0000e+000

vln = double(solve(vDc == vDcWanted))

vln =

76.9530e+000

vll = vln*sqrt(3)

vll =

133.2865e+000

% the line-to-neutral voltage must be adjusted to 77 V RMS

% this voltage will provide 133 V line-to-line and may be used to power a

% power brick (adapter) for the control circuitry

vPeak = vln*sqrt(2) % for diode selection

vPeak =

108.8280e+000

prospEff = 0.6; % prospetive efficiency

prospPow = 2e3;

gridPow = prospPow/prospEff

gridPow =

3.3333e+003

phaseCurr = gridPow/(3*vln)

phaseCurr =

14.4388e+000

iDc = gridPow/vDcWanted

iDc =

18.5185e+000

1 phi Rectifier For Control CCT

vAv_1phi = (2*sqrt(2)/pi)*vln

vAv_1phi =

69.2820e+000

In the simulations, it is assumed that efficiency is 60%. When the efficiency is assumed as 0.6, MOSFETs and diodes conducts 18.52A. Since rated current is 23.4A and simulations shows the current that diodes and MOSFETs conduct is 18.52, chosen physical semiconductors have current ratings greater or equal to 23A.

Since the motor will be driven with 180VDC, voltage ratings of the MOSFETs are chosen as 200V.

To provide constant 5VDC to control circuitries, LM2596 Buck Regulator, which have adjustable output voltage with ±4% ripple, is used. The output of the one of LM2595 is directly ESP8266. Output of the other LM2596 is utilized to provide isolated 12VDC by using ROE-0512S isolated converters. OpAmps, which is used for current sensing comparison to over current protection, require ±12VDC which is also created by two ROE-0512S.

## Physical Implementation

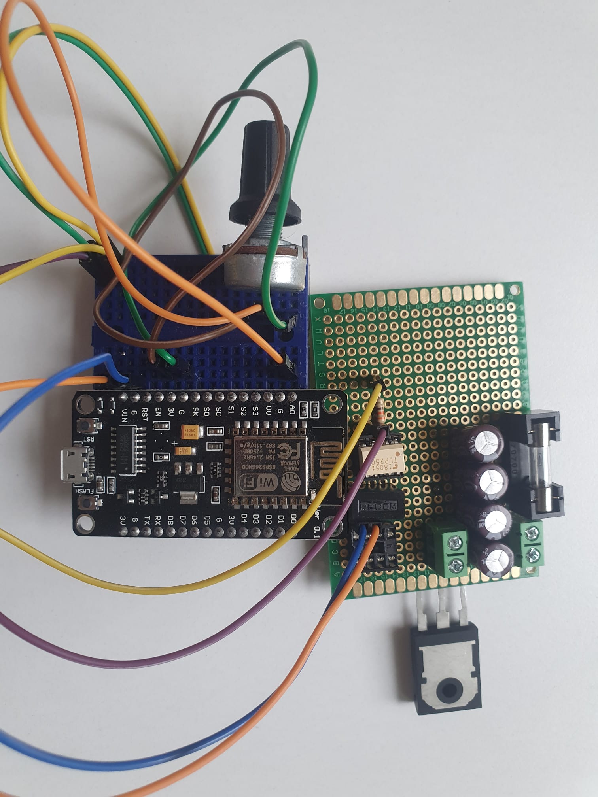
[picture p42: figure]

Figure 9: Buck Converter Circuit

Figure 9 show Buck Converter implementation, which is failed since in the simulation, capacitors don’t draw current. As a result, values are miscalculated.

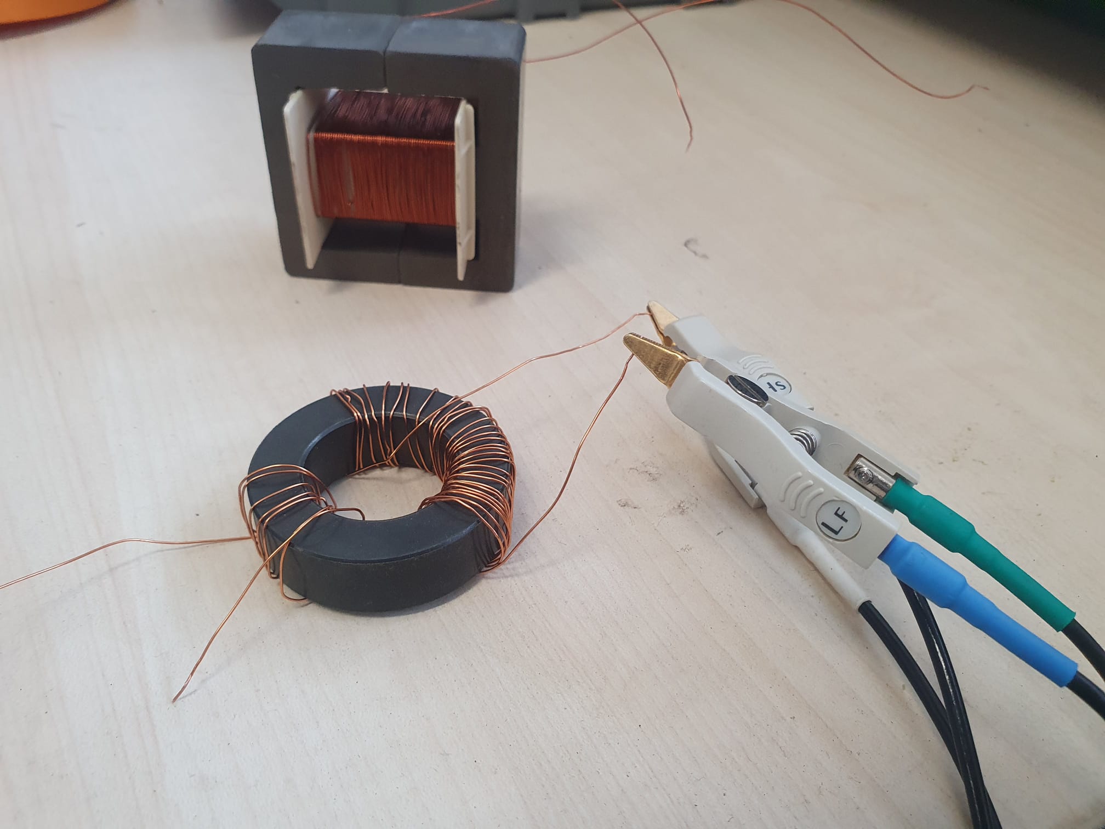
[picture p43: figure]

Figure 10: Manually Wounded Transformers

Figure 10 shows the transformer prototypes. Both transformers are failed. Toroidal core transformer is failed since inductance of the transformer is very small, which can be seen from Figure 11.


Figure 11: Inductance measurement of Toroidal Core Transformer

Even though the E core has higher number of windings, it stills draws very large current as shown in the Figure 12.


Figure 12: Current Measurement of Primary Side of E Core Transformer

Results of the experiments shows that more professionally designed transformed is required for step down transformer.

## Conclusion

In this report, bonuses, which effect the design of the project, topology and its explanation, component selection steps and experimental results are provided. Next step of the project is overhauling the miscalculated component parameters and construct the base circuitry, which is one quadrant simple MOSFET drive. Then, OpAmp circuities will be designed for current loop and H bridge four quadrant operation.

# References

[1] | C. AUTOMATION, "CANTHO AUTOMATION," 26 04 2022. [Online]. Available: https://canthoautomation.com/three-phase-full-wave-controlled-rectifier/.

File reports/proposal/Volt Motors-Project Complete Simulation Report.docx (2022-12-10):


# EE463 Static Power Conversion I

# Term Project Complete Simulation Report

## Volt Motors

## Mehmet Emre DOĞAN – 2374825

## Gamze ÇELİK – 2304327

## Ömer ŞEN – 2305415

## Introduction

In this project, a DC Motor Drive will be designed and implemented. The drive will run a DC motor when it is supplied by an AC source. In this report, aimed bonuses will be provided initially since the aims directs the topology. Then, Topology will be provided, and necessary simulation results will be given. Next, physical implementation work that has been done so far will be showed.

## Targeted Bonuses

### 1- Tea Bonus

One of the aimed bonuses it that providing 2kW for 5 minutes to boil a water and make an glass of hot tea.

### 2- PCB Bonus

An implementation of the system to a PCB is planned for not only the bonus points but also for building more robust system.

### 3- Efficiency Bonus

One of the goals is that constructing the most efficient circuit that fulfills the function. However, the bonus is not only depending on the circuit but also depends on the other groups circuits. Therefore, making the system as efficient as possible is the goal at that point.

### 4- Industrial Design Bonus

In order to protect the system from the outside impacts and crushes, it will be covered by a case.

### 5- Single Supply Bonus

The system is designed to supply only with a one AC source. Rest of the voltage level(s) will be obtained by inside converters.

### 6- Closed-Loop Voltage/Current Control Bonus

In order to protect the components from the high current, a closed feedback loop will be implemented by a current sensor.

### 7- Closed-Loop Speed Control Bonus

In order to obtain the speed of the motor and construct a speed control loop, an infrared sensor will be utilized.

### 8- Four-Quadrant Bonus

To operate in all the quadrants, 4 MOSFETs will be driven by 3 isolated drivers and OpAmp control.

## Topology


Figure 1: First Sheet of Topology


Figure 2: Second Sheet of Topology

Due to ease of usage of three phase full bridge rectifier + buck converter topology compared to other two topologies, three phase full bridge rectifier + buck converter is chosen as can be seen from the Figure 3. Moreover, the team is more experienced with the buck converter, which is another reason to choose buck converter topology. Also, implementing a topology which works in four of the quadrants, which is a determined feature by the team, would be very difficult by using thyristor. Therefore, H bridge topology is chosen to operate in four of the quadrants.

In order to supply the system with only one voltage source several converters are added to the topology, which can be seen from the Figure 1. Also, a transformer will be placed in the topology to provide required voltage level to the control circuitry. Output of the transformer will be rectified by a single-phase rectifier. After filtering, the closed loop buck converter which comes next will provide 5VDC output voltage.

Speed control feedback loop will be implemented by software that functions as PID. Input signal of the PID controller will be taken with infrared sensor.

Current control will be implemented by current sensor which will be connected in series to the armature terminals.


Figure 3: Thyristor Rectifier Circuit [1]

## Simulation Results


Figure 4: Simulation Circuitry

Basic purpose of the simulation is obtaining component ratings. The most important issue with the H bridge is determining the driving algorithm of the H bridge, which is hard to simulate in Simulink. As a result, H bridge is not implemented in Simulink.


Figure 5: Control Circuitry Input Voltage


Figure 6: Motor Terminal Voltage Before PWM Signal


Figure 7: Stability Simulation of Rectifiers


Figure 8: Terminal Rating of DC Motor After PWM Signal

## Component Selection

### Matlab Calculations

Base Calculation

clearvars

format shortEng

syms v_ln

vDc = (3*sqrt(6)/pi)*v_ln

vDc =

vDcWanted = 180

vDcWanted =

180.0000e+000

vln = double(solve(vDc == vDcWanted))

vln =

76.9530e+000

vll = vln*sqrt(3)

vll =

133.2865e+000

% the line-to-neutral voltage must be adjusted to 77 V RMS

% this voltage will provide 133 V line-to-line and may be used to power a

% power brick (adapter) for the control circuitry

vPeak = vln*sqrt(2) % for diode selection

vPeak =

108.8280e+000

prospEff = 0.6; % prospetive efficiency

prospPow = 2e3;

gridPow = prospPow/prospEff

gridPow =

3.3333e+003

phaseCurr = gridPow/(3*vln)

phaseCurr =

14.4388e+000

iDc = gridPow/vDcWanted

iDc =

18.5185e+000

1 phi Rectifier For Control CCT

vAv_1phi = (2*sqrt(2)/pi)*vln

vAv_1phi =

69.2820e+000

In the simulations, it is assumed that efficiency is 60%. When the efficiency is assumed as 0.6, MOSFETs and diodes conducts 18.52A. Since rated current is 23.4A and simulations shows the current that diodes and MOSFETs conduct is 18.52, chosen physical semiconductors have current ratings greater or equal to 23A.

Since the motor will be driven with 180VDC, voltage ratings of the MOSFETs are chosen as 200V.

To provide constant 5VDC to control circuitries, LM2596 Buck Regulator, which have adjustable output voltage with ±4% ripple, is used. The output of the one of LM2595 is directly ESP8266. Output of the other LM2596 is utilized to provide isolated 12VDC by using ROE-0512S isolated converters. OpAmps, which is used for current sensing comparison to over current protection, require ±12VDC which is also created by two ROE-0512S.

## Physical Implementation


Figure 9: Buck Converter Circuit

Figure 9 show Buck Converter implementation, which is failed since in the simulation, capacitors don’t draw current. As a result, values are miscalculated.


Figure 10: Manually Wounded Transformers

Figure 10 shows the transformer prototypes. Both transformers are failed. Toroidal core transformer is failed since inductance of the transformer is very small, which can be seen from Figure 11.


Figure 11: Inductance measurement of Toroidal Core Transformer

Even though the E core has higher number of windings, it stills draws very large current as shown in the Figure 12.


Figure 12: Current Measurement of Primary Side of E Core Transformer

Results of the experiments shows that more professionally designed transformed is required for step down transformer.

## Conclusion

In this report, bonuses, which effect the design of the project, topology and its explanation, component selection steps and experimental results are provided. Next step of the project is overhauling the miscalculated component parameters and construct the base circuitry, which is one quadrant simple MOSFET drive. Then, OpAmp circuities will be designed for current loop and H bridge four quadrant operation.

# References

[1] | C. AUTOMATION, "CANTHO AUTOMATION," 26 04 2022. [Online]. Available: https://canthoautomation.com/three-phase-full-wave-controlled-rectifier/.

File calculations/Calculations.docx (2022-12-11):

V_(DC) = (3×√6)/π×V_(ln)

V_(DC) = 180V

V_(ln) = 76.95V

V_(ll) =V_(ln) ×√3=133.29 V

V_(peak) = V_(ln) ×√2 = 108.83

Assumption: Efficiency = 60%

2000 W = 0.6 × Input Power

P_(in) = 3.33 kW = 180 V ×I_(DC)

I_(DC) = 18.5 A

I_(phase) = (P_(in))/(3×V_(ln))=14.43 A

P_(conduction,MOSFET) = R_(DS,on) ×I_(DC) ^2 =80mΩ×18.5A^2 =27.38W

P_(switching,MOSFET) =E_(Total,switching) × f_(sw) =330μJ×1000Hz=0.33W

P_(conduction,DIODE) =V_(F,ON) ×I_(DC) =1.52V×18.5A =28.12W

P_(switching,DIODE) =V_(Reverse) ×I_(rr) ×t_(rr) × 1/2×f_(sw) =1/2*350V*9A*150ns*1kHz=0.24W

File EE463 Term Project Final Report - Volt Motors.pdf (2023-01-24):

# EE463 Static Power Conversion I Term Project Final Report

## Volt Motors

## Mehmet Emre DOĞAN – 2374825 Gamze ÇELİK – 2304327

## Ömer ŞEN – 2305415

© 2022-2023

## Introduction

In this project, a DC Motor Drive will be designed and implemented. The drive will run

a DC motor when it is supplied by an AC source. In this report, the steps of component selection

will be given. Next, key points of design decisions will be provided. Then, computer

simulations with motor models will be provided with the test results of the system from demo

day and from previous tests that have been done so far will be shown. Finally, test results

thermal calculations will be done and compared with actual results.

## Component Selection

Table 1: Component and Price List

Component | Quantity | Price
IGBT - IXGH24N60C4D1 | 1 | 96
3 Phase FBR | 1 | 120
1000 μF 400V Capacitor | 1 | 200
LM2596 | 2 | 32.14
230:24 Transformer | 1 | 252
Single Phase FBR | 1 | 2.45
2200 μF Capacitor | 2 | 140
TLP250 | 1 | 47.92
330Ω Resistor | 2 | 0.88
ESP8266 | 1 | 75.94
ROE-0512 | 1 | 89.71
DSEI30-06A | 1 | 33.08
Current Sensor - ACS712 | 1 | 47.26
Fuse | 2 | 1.34
Heatsink | 3 | 45
Fan | 2 | 56
Voltmeter | 3 | 162
Lamp | 1 | 20
Banana Connector | 6 | 49
Terminal Block | 8 | 22.7
Box | 2 | 150
Stripboard | 2 | 25.83
Deep Socket | 3 | 1.98

Switch | 1 | 4.73
Total | | 1535,96

IGBT - IXGH24N60C4D1

One of the main components is IGBT used in the buck converter. IXGH24N60C4D1 has an

appropriate rating for the application. Moreover, the main reason for choosing

IXGH24N60C4D1 is that it is easy to access since there are many of them in the stock of the

laboratory.

### 3 Phase FBR

The chosen model is compliant to the system with its ratings. However, the main reason to

choose the rectifier is the type of its sockets. Its sockets are compatible with the cable terminals

in the laboratory. It would be easier to replace it in case of failure.

1000 μF 400V Capacitor

In simulations, 1000uF provided decent enough ripple for the high voltage circuitry, when the

rated current of the motor is drawn. Moreover, the 400V rating was chosen to be safe to the

possible ringing may occur in the voltage.

LM2596

There is a need for creating 5VDC 12VDC low voltages for the MCU and cooling fans,

respectively. Moreover, this stepping down operation needs to be in a regulated manner. The

LM2596 has a built-in feedback mechanism, regulating the voltage to desired value.

Furthermore, LM2596 Adjustable modules are cheap and easy to access. As a result, it is

chosen.

230:24 Transformer

Using only one supply is a bonus to obtain that transformer is chosen. The ratio is chosen based

on the required voltage at the secondary of the transformer.

Single Phase FBR

In order to convert stepped down AC voltage by transformer into dc voltage, a rectifier is

required. Due to easy access and low-price compliant ratings, KBU2M is chosen.

2200 μF Capacitor

In simulations, 2x2200uF provided decent enough ripple for the low voltage adapter circuitry.

TLP250

To isolate the MCU and High voltage side, an Opto isolator is needed. Since this model was

available in the lab, it was chosen.

330Ω Resistor

To limit the current and the voltage which goes into the LED side of an optocoupler, a

resistance is required. According to the calculations 330-ohm was appropriate.

ESP8266

ESP8266 is used instead of an Arduino because it is cheaper, has wi-fi, has higher memory,

has a higher core frequency, compatible with Arduino IDE, and lastly, it supports PWM at all

pins. There are various MCUs available. However,

ROE-0512

For optocoupler isolated 12V is needed. To convert 5V to isolated 12V ROE-0512 was a perfect

choice.

DSEI30-06A

DSEI-30-06A is a good option for our design with its price, ratings, and accessibility.

Current Sensor - ACS712

Initially current feedback is designed, and the system is designed according to it. However,

during the implications, the sensor fails, yet it conducts the current that is supposed to.

Therefore, it is not utilized but not removed.

Fuse

Different levels of fuses are used to protect our circuit against high currents and bugs due to

the high currents.

Heatsink & Fan

Heatsinks and fans were used for cooling. Some components can reach high temperatures and at those temperatures, components do not operate properly. There is a video link to one of the tests showing the effect of the fan on the IGBT and the diode of the main buck converter. https://youtu.be/r-FZcK4Lljk

Voltmeter

To read input voltages voltmeters were used. Used voltmeters have 20 - 500 V AC range.

Lamp

When the output is active the lamp is on to notify the user.

Banana Connector

For easy I/O connections banana connectors were used.

Terminal Block

To obtain a modular system, we prefer to use them. Also, it makes it easy to mount/unmount

the subsystems.

Box

To provide safe and easy usage to the user, and also for aesthetic reasons.

Dip socket

It was placed because if TLP250 breaks it can be changed easily. Also, during the soldering

process, TLP250 can also break due to high temperature so that dip socket was used.

Switch

Switch is used to power the ESP8266 since ESP8266 requires 5V to operate without booting

bugs. To prevent these bugs a switch was used.

# Design Decisions

As we discussed in the complete simulation report, we will use the topology consisting

of a three-phase full bridge rectifier feeding a buck converter that eventually drives the motor.

The main block diagram of the system is shown in Figure 1 and Figure 2. Moreover, to

accomplish various bonuses, we have some other submodules.

The motor drive system is designed in a modular manner to make it easy to analyze and

debug. As well as to avoid epic failures; for example, a total board failure due to the explosion

caused by an arc born from not enough clearance in the AC mains line. Thanks to the modular

approach, we were able to get rid of only the faulty parts and redesign only them, not the

complete system.

Hence, the motor driver system consists of various subsystems, as the block diagrams

suggest. Each subsystem will be handled in detail to guarantee the subsystems work properly

not only standalone but also after the integration.

In Figure 3, the completely integrated and finished version of the system is shown.


Figure 1: Main block diagram sheet 1


Figure 2: Main block diagram sheet 2

Figure 3: The completely integrated system from the demo day

## AC-DC Converter Subsystem

To drive the DC motor, we need DC power. Moreover, to run the MCU (Micro-

Controller-Unit) we also need low-power DC voltage, which needs to be isolated from the

mains DC power.

3-Phase Full Bridge Rectifier + Capacitor

This rectifier, shown in Figure 4, rectifies the main AC power provided from the variac

to DC 200V. Although the rated voltage of the motor is 180V DC, we rectify it to 200V DC

because we plan to reach the rated voltage at 90% duty cycle. The discussion of why is provided

in the Duty Cycle subsection of the MCU section. Then the voltage is smoothened (decreased

its ripple) by the 1mF 400V polarized aluminum capacitor, shown in Figure 5, connected to the

exit of the 3-Phase FBR.


Figure 4: The 3-Phase FBR


Figure 5: The Main Capacitor

Low Power Adapter

The low-power adapter schematic is shown in Figure 6. Its job is to provide low DC

voltage to the LM2596 buck regulators to power MCU, fans, sensors, optoisolator, and other

low-power devices.


Figure 6: Low Power Adapter Schematic

This adapter, first, steps down the voltage using the transformer, then rectify with the

single-phase FBR. Afterward, thanks to the large capacity of aluminum capacitors, the output

ripple is smoothened. Moreover, in design, 2 ceramic capacitors are put to decrease the

equivalent ESR of the subsystems of capacitors. However, these are not soldered in

implementation since we did not have an ESR problem.

The fuse provides overcurrent protection and screwed terminal connectors ease making

cable connections.

The VCC provided by this adapter is expected to be near 20VDC when two AC lines

from the variac are connected to its AC_IN. Note that, the variac is adjusted to 85 V AC line

to neutral, resulting in 148 V AC line to line.

However, since the transformer is nearly unloaded, due to the low-power devices

connected, this output voltage is expected to increase. However, thanks to the 36 V DC

maximum input voltage and built-in feedback and filter system of LM2596 buck regulator

modules, neither this voltage rise nor the ripples are a problem. LM2596 modules provide clean

and consistent voltages to MCU and other low-voltage peripherals.

The PCB design and an image from the demo day are shown for the adapter in Figure

7 and Figure 8, respectively.


Figure 7: The low-power adapter PCB


Figure 8: The low-power adapter from the demo day

## Main Buck Converter Subsystem

The main buck converter’s schematic is shown in Figure 9. The schematic includes 5

VDC and GND busbars to power the peripherals.

The output of the 3-Phase FBR is connected to the board using screw terminals. This

voltage is filtered out via a 1 mF 400V aluminum capacitor, shown in Figure 5. The additional

10 nF ceramic capacitor is added to the design in case we had an ESR problem. But in

implementation, it is not soldered since we had no ESR problems. Then this voltage passes a

protective fuse and is called VCC, or VCC_PWR.

The isolated DC-DC converter creates an isolated +12VDC from the mains 5VDC to

feed into the optocoupler’s VCC and GND.

The optoisolator receives the PWM signal from the ESP and amplifies it in an isolated

manner to drive the gate of the IGBT. 330 Ohm of resistors is connected in series to the LED

part of the Opto to limit current. The Opto’s forward voltage is near 1.8 Volts and this resistor

guarantees the ESP provides current to the Opto less than 10 mA.

The resistor between the Opto’s output and the gate of the IGBT is also 330 Ohms

because it works. We first tried 330 Ohm and it worked perfectly, then we did not change it.

The freewheeling diode parallel to the output of the converter makes sure the current

due to the inductance of the motor can have a path to circulate when the IGBT is on OFF duty.

Therefore, the IGBT is protected from damages due to overvoltage caused by the motor

inductance.

The current sensor is connected via the screw terminals to measure the current drawn.

The screw terminals ease the change of the sensor in case of failure.


Figure 9: main Buck Converter


Figure 10: The failed main buck PCB

We designed a PCB for the Main Buck Converter, as shown in Figure 10. However, it

failed due to some known and unknown reasons.

One of the known reasons is that the PCB has been wrongly produced. The positive pin

of the Opto’s LED is shorted to the ground because of a manufacturing error. The error is

understood by comparing Figure 11 with Figure 10.


Figure 11: The Opto LED positive input, manufactured


Figure 12: The Opto LED inputs, designed

Although we solved this problem by bending the optoisolator’s LED pins and space

soldered these pins. However, unfortunately, the board was still not working due to the errors

we were unable to diagnose. Afterward, we rebuilt the buck circuit on the stripboard before the

demo, as shown in Figure 13.

Thanks to the modularity approach, we were able to use the rest of the designs without

any problems.


Figure 13: The buck converter on the stripboard

## MCU & Software Subsystem

The MCU subsystem is responsible to generate the PWM signal with the duty cycle

that the users select via the modern Web GUI (Graphical User Interface), as shown in Figure

14. Moreover, as shown in Figure 14, the software has a WebSerisal to print timestamped

important run-time data.

The online Web GUI demo is available [1]. Note that the Set Direction and Close Loop

menus are inactive due to the system not including H-Bridge and Close Loop Speed Sensor.

However, these menus exist for future versions of our design updates.


Figure 14: WebGui with WebSerial from demo day

Duty Cycle

The duty cycle is adjusted using the slide bar shown in Figure 15. The range of the used

duty cycle is 0.1-0.9. That is, the motor reaches its rated speed and power with the duty cycle

at 90%, instead of 100%. The reason for that approach is to avoid unstable switching at 0%

(fully off) and 100% (fully on) by providing a safety margin. For example, due to

environmental noise, the PWM signal may deviate slightly from the adjusted duty, and the

safety margin makes sure this deviation will not change the state of the system.


Figure 15: Open-loop duty selector slide-bar

Ramping Duty Cycle

The duty cycle is slowly increased and decreased to avoid the inrush currents in the

motor starting as well as to decrease the effect of transient spikes that may be caused by fastly

changing the duty cycle. This operation has a video demo [2], and a scene from this video is

shown in Figure 16.


Figure 16: YouTube: ESP8266 Ramp PWM via Web GUI

Switching Frequency

The switching frequency of the generated PWM signal is chosen as 1 kHz since the

Main Buck Converter uses an IGBT to switch the motor. We know that the IGBTs are not

capable of switching at high frequencies due to their high-rise time and turn-on/off delay times,

in addition to their huge switching energy. For example, we used IXGH24N60C4D1 N channel

IGBT, whose switching energy is 1.46 mJ. On the other hand, LSIC1MO120E0080 N Channel

SiC MOSFET only has 0.25 mJ of switching energy.

Moreover, designing a circuity capable of high switching frequency requires more

attention and expertise. For example, the paths carrying the PWM signal should be properly

engineered. However, due to our modular approach, we use jumper cables to carry the PWM

signal.

As a result, on the first try, we used 1 kHz as the switching frequency. Afterward, we

continued with that frequency because the integrated whole system worked pretty decent with

a 1 kHz frequency.

Power

The used board NodeMcu ESP8266 needs +5VDC from its Vin pin. The required

voltage is supplied by an LM2596 buck regulator. Moreover, a small switch is attached in series

to avoid booting bugs caused by the slowly increasing variac voltage. Thanks to that switch,

we power on the ESP manually when the variac voltage reaches its rated value.

Current Sensor

ACS712 Current sensor measures the motor current for debug purposes. Unfortunately,

the existing ACS712 was burned due to misconnections, and replaced with another. However,

since the current scale of the new one is different, the reading is wrong. The code needed to be

updated but since it was the last day, we do not want to cause further bugs by editing the code,

we did not edit.

In the future, a current feedback loop control could be added by just a software update

thanks to the current sensor.

Voltage Divider

To convert the 5 V analog level of the current sensor to the 3.3 V analog level of the

ESP, a resistor divider network is used.

## Display & Measurement Subsystem

This subsystem consists of three voltmeters connected in a wye configuration to

measure line-to-neutral input voltages. Moreover, a signal lamp is connected to the output to

signal when the output is enabled.

## Cooling Subsystem

This subsystem consists of two 12V DC fans. One for cooling the three-phase rectifier,

one for the IGBT and diode of the Main Buck Converter.

## Computer Simulations and Test Results


Figure 17: Transformer Simulation Schematic


Figure 18: Transformer Simulation Results


Figure 19: Transformer Test Result for VLL,rms=130V

In the simulations, it has been found that expected output voltage of the single supply

transformer system is around 22.4 Volt DC. During the implementation, tests show that the

implemented system provides approximately 22.4 Volt, which is almost the same. Output

rectified voltage is provided to LM2596 Adjustable Voltage Step Down Power Module (4-35V

Input - 1-30V Output) in order to provide power to lover voltage components, such as fans,

controllers.


Figure 20: Output Voltage and Armature Current for Rated Voltage

Figure 21: Average and Waveform Graphs for Output Voltage and Armature Current at

Rated Voltage


Figure 22: Armature Current Waveform

Figure 23: Voltage and Power Ratings for Rated Voltage

Previous 4 Figures, Figure 20 to 23, show the simulation and test results of rated voltage of the

system without load. Figure 20 simulation results show the output voltage average as 184.6V and Figure 23 show the actual test results which show output line to line voltage as 130V. For

130V line to line input voltage, output voltage can be seen from Figure 22. Peak of the purple

graph is around 200V and the duty cycle is 0.9. Therefore, output average voltage is around

180V, which is expected from the simulation result Figure 20. The Figure 21 shows the

simulation results for the waveforms. Notice that the current waveform is scaled with 0.1A. As

can be seen from the test results at Figure 22, test results and simulation results are compliant

with each other. The efficiency is found as 0.340kW/0.364kW=94% during the tests.


Figure 24: Output Voltage and Armature Current for 2kW Power


Figure 25: Average and Waveform Graphs for Output Voltage and Armature Current at 2kW

Figure 26: Armature Current Waveform


Figure 27: Voltage and Power Ratings for 2kW Power

Previous 4 Figures, Figure 24 to 27, show the simulation and test results of the system

at 2kW Power input. Figure 24 simulation results show the output voltage around 180V and

Figure 27 show the actual test results which show output line to line voltage as 160V. For 160V

line to line input voltage, output voltage can be seen from Figure 26. Unfortunately, there is no

clear view of the output voltage waveform. However, it is known that output voltage is around

180V. The test results are a bit different from the simulation results, which have input line to

line voltage as 130V. The reason behind this difference is that when drawn current increases,

the capacitance of the capacitor becomes insufficient, and ripples are increased. To provide the

same output voltage and eliminate the negative effects of the ripples, input voltage is increased.

Therefore, output average voltage is around 180V for a higher input voltage. The Figure 25

shows the simulation results for the waveforms. Notice that the current waveform is scaled

with 0.1A. As can be seen from the test results at Figure 26, test results and simulation results

are compliant with each other. The efficiency is found as 1.911kW/1.982W=96% during the

tests.

## Thermal Calculations

Ploss,conduction,IGBT = VCE,sat ∙ Iavg ∙ Duty ≅ 1.9V ∙ 10.4A ∙ 0.9 = 17.784W

Ploss,switcℎing,IGBT = Eswitcℎing,total ∙ fswitcℎing ≅ 1.46mJ ∙ 1kHz = 1.46 W

Ploss,total,IGBT = 19.244W

Ploss,conduction,diode = Vfwd ∙ Iavg ∙ (1 − Duty) ≅ 1.52V ∙ 10.4A ∙ 0.1 = 1.58W

Ploss,switcℎing,diode = (

1
2
- CR ∙ VR

2 +

1
6
- IRR ∙ VR ∙ tb) ∙ fswitcℎing

≅ (

1
2
- 2pF ∙ 600V

2 +

1
6
- 9A ∙ 600V ∙ 150ns/2) ∙ 1kHz = 0.068 W

Ploss,total,diode = 1.648W

Tjunction = Tambient + Ploss ∗ Rtℎ,eq

TIGBT = Tambient + Ploss ∗ (Rtℎ,JC + Rtℎ,HA) = 17°C + 19.24W ∗ (3.5°C/W + 0.8°C/W)

= 99.3°C

TDiode = Tambient + Ploss ∗ (Rtℎ,JC + Rtℎ,CH + Rtℎ,HA )

= 17°C + 1.648W ∗ (0.8°C/W + 0.25°C/W + 3.5°C/W) = 24.5°C


Figure 28: Thermal View of The Main Lossy Components

As can be seen from the Figure x, the IGBT reaches the temperature 105°C, which is

calculated as 99.3°C in the calculations. The reason for the difference is that the thermal

resistance between case to heatsink is not specified in the datasheet; therefore, missing

components of the thermal resistance equivalent results as a minor difference between

calculations and actual results. For the diode, calculated temperature is observed during the

2kW operation, which is expected.

# Conclusion

In conclusion, the project aimed to design and implement a DC Motor Drive that could

run a DC motor when supplied with an AC source. The report discussed the design decisions

and bonus topologies used, such as the single supply bonus, PCB bonus, TEA bonus, and Box

bonus, as well as providing computer simulations of the motor models. The process of

component selection was also outlined, and test results from both demo day and previous tests

were presented. These added bonuses have helped to increase the functionality and efficiency

of the DC Motor Drive. Overall, the project was a success in achieving its goal of creating a

functional and enhanced DC Motor Drive.

# References

[1] M. E. Doğan, "ESP Webdemo," 2022. [Online]. Available: https://medogan.com/test_server_demo/463_esp_webdemo.html
[2] M. E. Doğan, "ESP8266 Ramp PWM via Web GUI," 2022. [Online]. Available: https://www.youtube.com/watch?v=6NDupYknA6s.
[3] G. Çelik, EE463 - Term Project Demo Video” 2023. [Online]. Available: https://youtu.be/3Q_IF74OBMI

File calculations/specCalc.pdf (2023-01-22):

### Base Calculation

clearvars
format shortEng

syms v_ln
vDc = (3*sqrt(6)/pi)*v_ln

vDc =

maxDuty = 0.9

maxDuty =
900.0000e-003
vDcWanted = 180/maxDuty

vDcWanted =
200.0000e+000
vln = double(solve(vDc == vDcWanted))

vln =
85.5033e+000
vll = vln*sqrt(3)

vll =
148.0961e+000
% the line-to-neutral voltage must be adjusted to 77 V RMS
% this voltage will provide 133 V line-to-line and may be used to power a % power brick (adapter) for the control circuitry
vPeak = vln*sqrt(2) % for diode selection

vPeak =
120.9200e+000

prospEff = 0.6; % prospetive efficiency prospPow = 2e3;
gridPow = prospPow/prospEff

gridPow =
3.3333e+003
phaseCurr = gridPow/(3*vln)

phaseCurr =
12.9949e+000
iDc = gridPow/vDcWanted

iDc =
16.6667e+000

1

### 1 phi Rectifier For Control CCT

vAv_1phi = (2*sqrt(2)/pi)*vln

vAv_1phi =
76.9800e+000

2

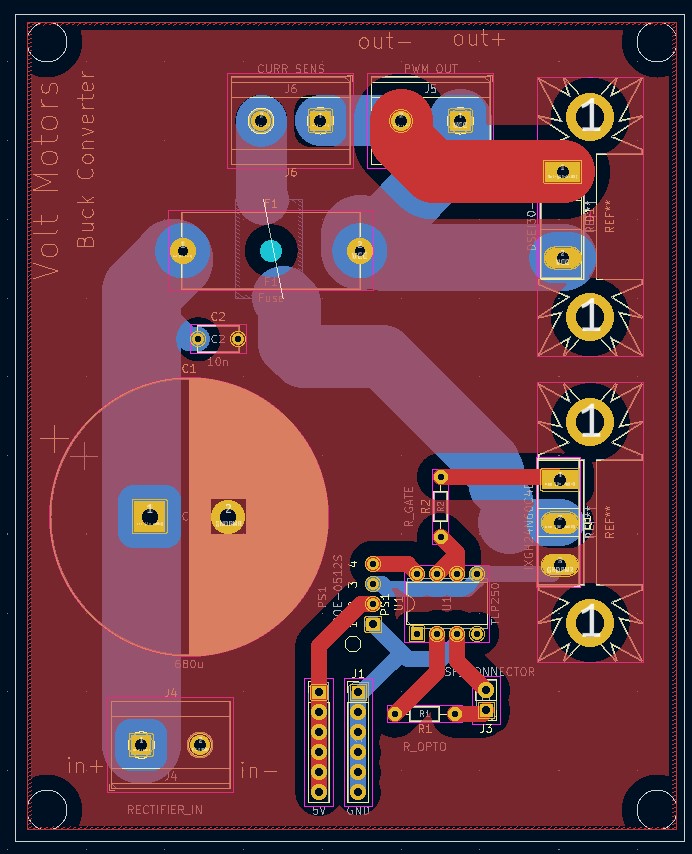
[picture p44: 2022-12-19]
pcbDesigns/buck/buck/pics/fb.jpg

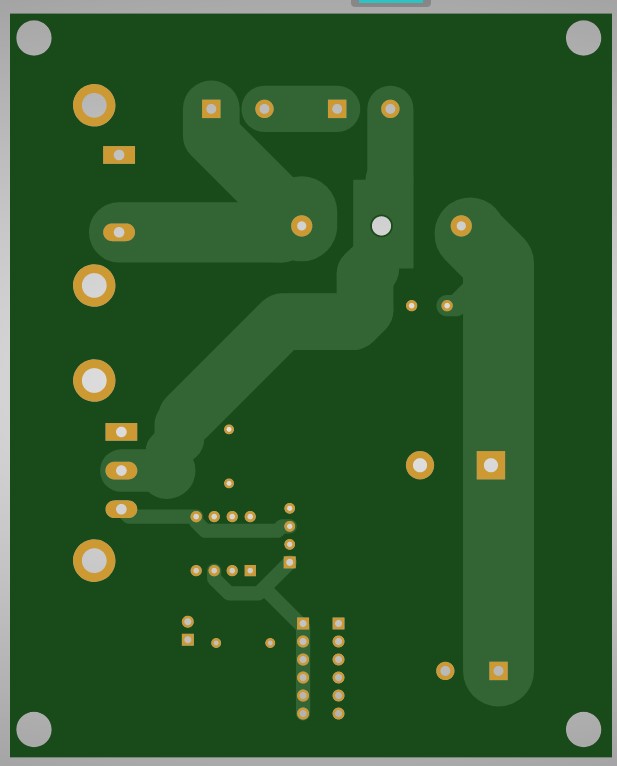
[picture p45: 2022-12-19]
pcbDesigns/buck/buck/pics/back.jpg

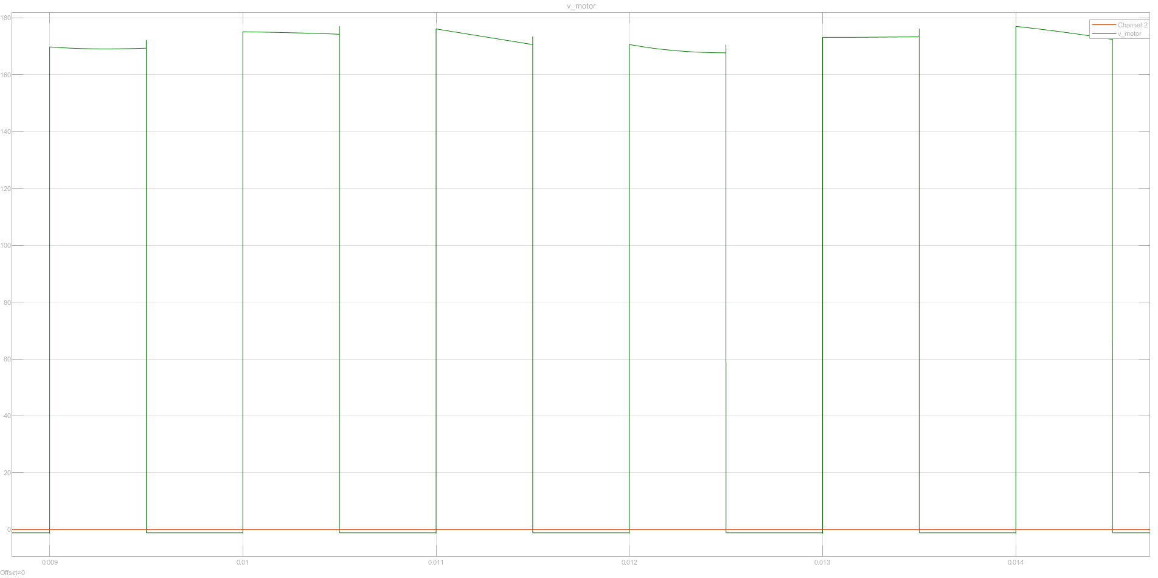
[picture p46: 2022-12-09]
reports/proposal/pics/motorModelPwmClose.png

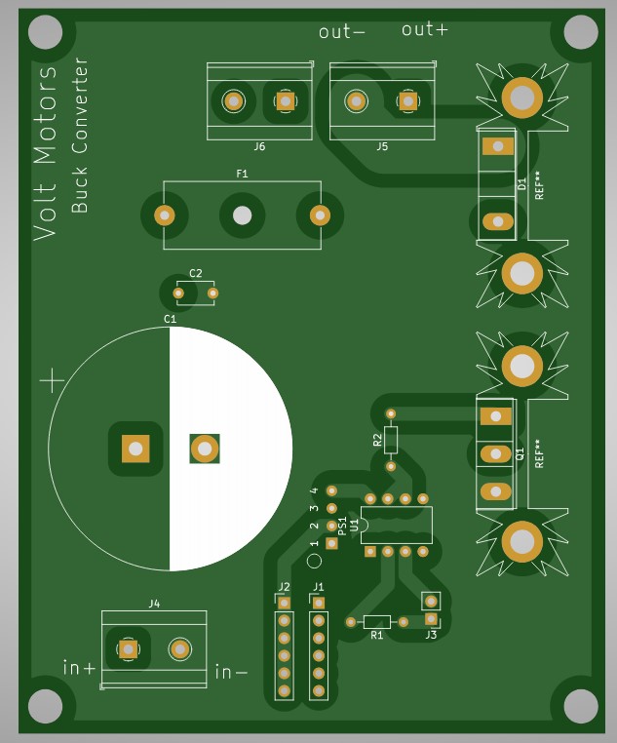
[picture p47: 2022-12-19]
pcbDesigns/buck/buck/pics/front.jpg

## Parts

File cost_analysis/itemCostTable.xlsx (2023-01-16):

item | link | usdPrice_USD | basePrice_TL | tax_percent | count | totalPrice_TL | boughtByEmre
13x25cm Delikli Plaket | https://www.motorobit.com/urun/13x25cm-delikli-plaket | - | 22.5 | 1.18 | 1 | 26.55 | 1
Termoplastik Buat (Büyük) | Bauhaus | - | 115 | 1 | 1 | 115 | 1
Termoplastik Buat (Küçük) | Bauhaus | - | 35 | 1 | 1 | 35 | 1
1G 2.5 NYA Cable (Red) | Bauhaus | - | 15 | 1 | 0.3 | 4.5 | 1
1G 2.5 NYA Cable (Black) | Bauhaus | - | 15 | 1 | 0.3 | 4.5 | 1
1G 1.5 NYA Cable (Red) | Bauhaus | - | 9.5 | 1 | 0.5 | 4.75 | 1
1G 1.5 NYA Cable (Black) | Bauhaus | - | 9.5 | 1 | 0.5 | 4.75 | 1
1G 1.5 NYA Cable (Brown) | Bauhaus | - | 9.5 | 1 | 0.2 | 1.9 | 1
1G 1.5 NYA Cable (Blue) | Bauhaus | - | 9.5 | 1 | 0.2 | 1.9 | 1
1G 1.5 NYA Cable (Yellow Green) | Bauhaus | - | 9.5 | 1 | 0.2 | 1.9 | 1
2G 0.75 TTR Cable white | Bauhaus | - | 9.5 | 1 | 0.5 | 4.75 | 1
3 Pinli Klemens | https://www.motorobit.com/urun/3-pinli-klemens | - | 2.22 | 1.18 | 1 | 2.6196 | 1
IRFP460 - 500V 20A Mosfet - TO247 | https://www.motorobit.com/urun/irfp460-500v-20a-mosfet-to247 | - | 26.18 | 1.18 | 1 | 30.8924 | 1
IRFP254 - 250V 23A Mosfet - TO247 | https://www.motorobit.com/urun/irfp254-250v-23a-mosfet-to247 | - | 23.375 | 1.18 | 1 | 27.5825 | 1
TO247 Metal Soğutucu Heatsink 25x34x12mm | https://www.motorobit.com/urun/to247-metal-sogutucu-heatsink-25x34x12mm | - | 11.22 | 1.18 | 3 | 39.7188 | 1
8x12cm Epoxy Çift Taraflı Delikli Plaket | https://www.motorobit.com/urun/8x12cm-epoxy-cift-tarafli-delikli-plaket | - | 25.2 | 1.18 | 1 | 29.736 | 1
5x5 cm Delikli (Bakır) Pertinaks Tek Yüzlü | https://www.robotistan.com/5x5-cm-delikli-pertinaks-tek-yuzlu | - | 3.33 | 1 | 1 | 3.33 | 1
KCD1 Mavi Nokta Işıklı On-Off Anahtar 12V | https://www.motorobit.com/urun/kcd1-mavi-nokta-isikli-on-off-anahtar-12v-ic132a | - | 4.73 | 1.18 | 1 | 5.5814 | 1
DSEI30-06A 37A 600V 35ns Hızlı Diyot | https://www.motorobit.com/urun/dsei30-06a-37a-600v-35ns-hizli-diyot | - | 33.08 | 1.18 | 1 | 39.0344 | 1
Mini Ayarlanabilir 3A Voltaj Regülatör Kartı - LM2596-ADJ | https://www.motorobit.com/urun/mini-ayarlanabilir-3a-voltaj-regulator-karti-lm2596-adj | - | 16.07 | 1.18 | 1 | 18.9626 | 1
M3 50 mm YSB Yıldız Silindirik Baş Metrik Vida - 10 Adet | https://www.robotistan.com/m3-50mm-ysb-yildiz-silindirik-bas-metrik-vida-10-adet | - | 4.2 | 1 | 0.4 | 1.68 | 1
8 Pin Dip Soket | https://www.robotistan.com/8-pin-dip-soket | - | 0.66 | 1 | 3 | 1.98 | 1
KF301V 5.0-2P | https://www.robotistan.com/kf301v-5 | - | 1.32 | 1 | 2 | 2.64 | 1
22 AWG Yellow | https://www.robotistan.com/montaj-kablosu-rulosu-22awg-15mt-cok-damar-sari | - | 0.9344444444 | 1 | 0.5 | 0.4672222222 | 1
23 AWG Green | https://www.robotistan.com/montaj-kablosu-rulosu-22awg-15mt-cok-damar-sari | - | 0.9344444444 | 1 | 0.5 | 0.4672222222 | 1
24 AWG Black | https://www.robotistan.com/montaj-kablosu-rulosu-22awg-15mt-cok-damar-sari | - | 0.9344444444 | 1 | 0.75 | 0.7008333333 | 1
Mini Soğutucu (A4988 ile Uyumlu) | https://www.motorobit.com/urun/mini-sogutucu-a4988-ile-uyumlu | - | 2.27 | 1.18 | 2 | 5.3572 | 1
680 uF 400 V Elektrolit Kondansatör | https://www.robotistan.com/680uf-400v-elektrolit-kondansator | - | 116.48 | 1 | 1 | 116.48 | 1
Male Header | https://www.robotistan.com/1x40-180-15mm | - | 0.072 | 1 | 14 | 1.008 | 1
Various Jumpers | https://www.robotistan.com/40-pin-ayrilabilen-disi-erkek-m-f-jumper-kablo-200-mm | - | 0.51575 | 1 | 15 | 7.73625 | 1
KBU2M - 2A 1000V Tarak Tip Köprü Diyot | https://www.motorobit.com/urun/kbu2m-2a-1000v-tarak-tip-kopru-diyot | - | 2.08 | 1.18 | 1 | 2.4544 | 1
2 Pin Bariyer Klemens - 7.62mm KF25C | https://www.motorobit.com/urun/2-pin-bariyer-klemens-7-62mm-kf25c-7-62 | - | 2.84 | 1.18 | 6 | 20.1072 | 1
Impact 22MM LED Sinyal Lambası Beyaz | https://www.hepsiburada.com/impact-22mm-led-sinyal-lambasi-beyaz-p-HBCV00002R1UER?magaza=ESİL%20ELEKTRİK | - | 20 | 1 | 1 | 20 | 1
Tianyi Dijital Voltmetre Ac 20-500V | https://www.hepsiburada.com/tianyi-dijital-voltmetre-ac-20-500v-p-HBCV00002Z4MRY?magaza=ESİL%20ELEKTRİK | - | 54 | 1 | 1 | 54 | 1
Tianyi Dijital Voltmetre Ac 20-500V | https://www.hepsiburada.com/tianyi-dijital-voltmetre-ac-20-500v-p-HBCV00002Z4MRX?magaza=ESİL%20ELEKTRİK | - | 54 | 1 | 1 | 54 | 1
Tianyi Dijital Voltmetre Ac 20-500V | https://www.hepsiburada.com/dijital-voltmetre-ac-20-500v-p-HBCV000030JEO4?magaza=ESİL%20ELEKTRİK | - | 54 | 1 | 1 | 54 | 1
ACS712 Akım Sensörü - Current Sensor Carrier -30 to +30 A | https://www.robotistan.com/acs712-akim-sensoru-current-sensor-carrier-30-to-30a | - | 47.26 | 1 | 1 | 47.26 | 1
 |  |  |  |  |  | 793.2960278

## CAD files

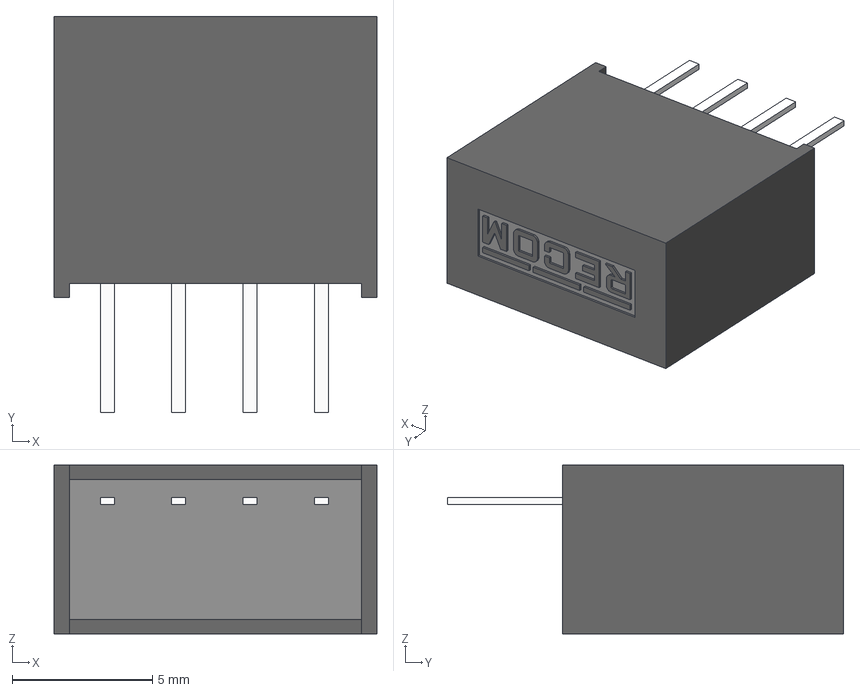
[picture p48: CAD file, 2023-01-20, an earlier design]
pcbDesigns/deprecated/hBridge/hBridge/ROE-0512S.step
11.5 x 14.1 x 6.00 mm

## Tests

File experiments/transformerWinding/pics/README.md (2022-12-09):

# DIY Transformer Winding Experiment
## Introduction 
&nbsp;&nbsp;&nbsp;&nbsp; To power our driver with only one supply, we need to decrease the supply voltage for the control circuitry. It is preferable to step down the AC input voltage before it is rectifed for the motor and rectify the low voltage afterward. This is because not only DC-DC buck converters have limited input voltage ratings but also isolating the motor from the control circuitry reduce the noise.

&nbsp;&nbsp;&nbsp;&nbsp; As a result, we tried to make our transformer using the cores and winding cables found at the laboratory.

## Toroidal Core
&nbsp;&nbsp;&nbsp;&nbsp; First we wound a transformer using a toroidal core. Since its number of turns were pretty less, the flux leakage was too high and the output voltage was way more than the expected.

<div><center>

### Winding
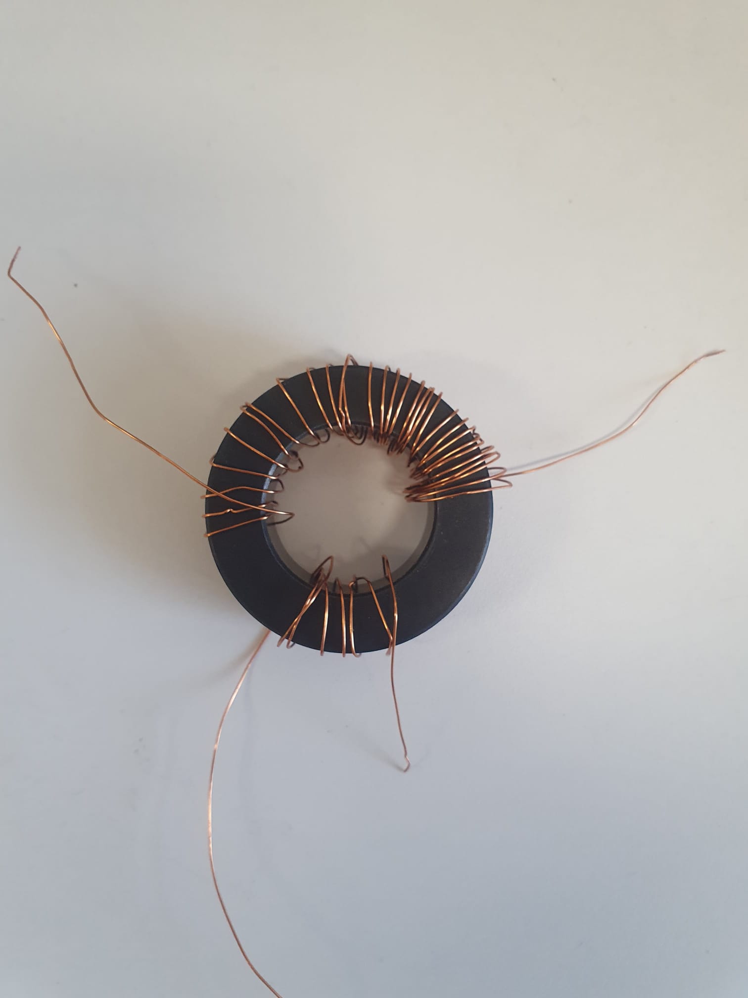
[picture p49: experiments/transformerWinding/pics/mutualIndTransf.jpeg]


### Inductance Measurement at Primary
tr

### Inductance Measurement at Primary [Results]
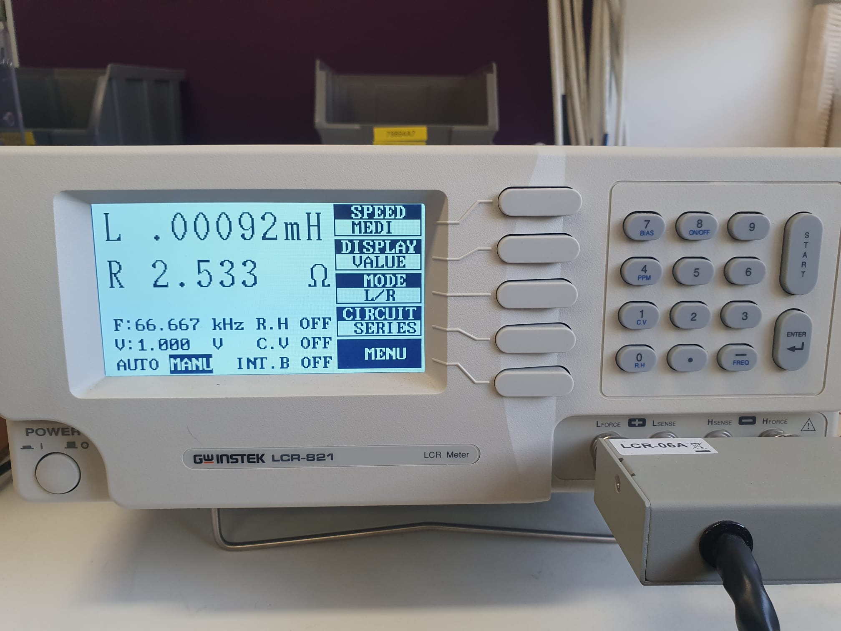
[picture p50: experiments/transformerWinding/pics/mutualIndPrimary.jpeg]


<center></div>

As a result, this component is useless as a transformer. 

## Double E Core
&nbsp;&nbsp;&nbsp;&nbsp; Second, a transformer is wound by using the E cores. This time, the number of turns were increased, but the magnetizing inductance of the transformer was not enough, causing a lot of current to flow even at no load. However, the voltage input-output characteristics was consistent with the expectations.

<div><center>

### Winding
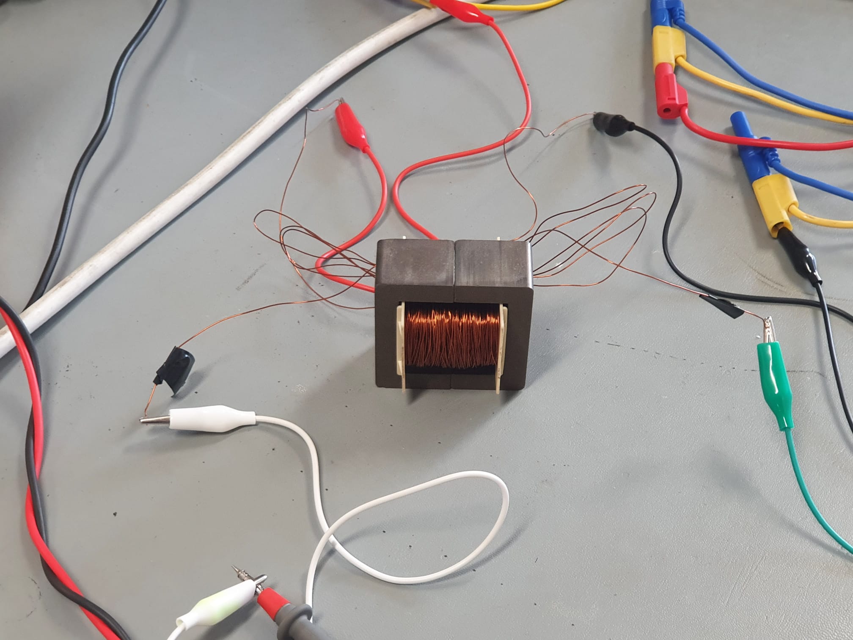
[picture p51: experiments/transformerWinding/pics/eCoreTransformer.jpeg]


### Test Setup
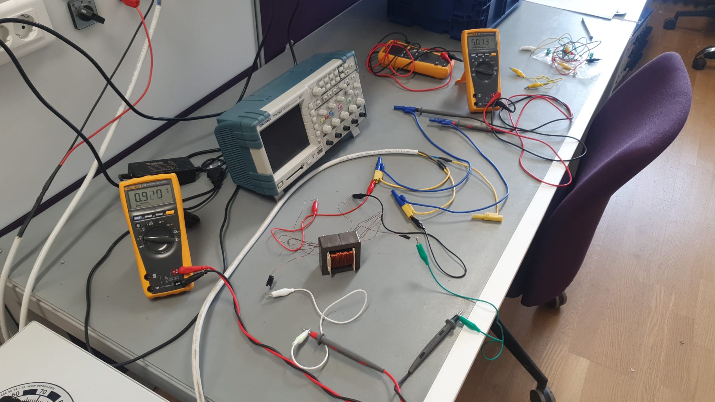
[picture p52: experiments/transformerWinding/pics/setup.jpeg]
setup


### Primary Voltage
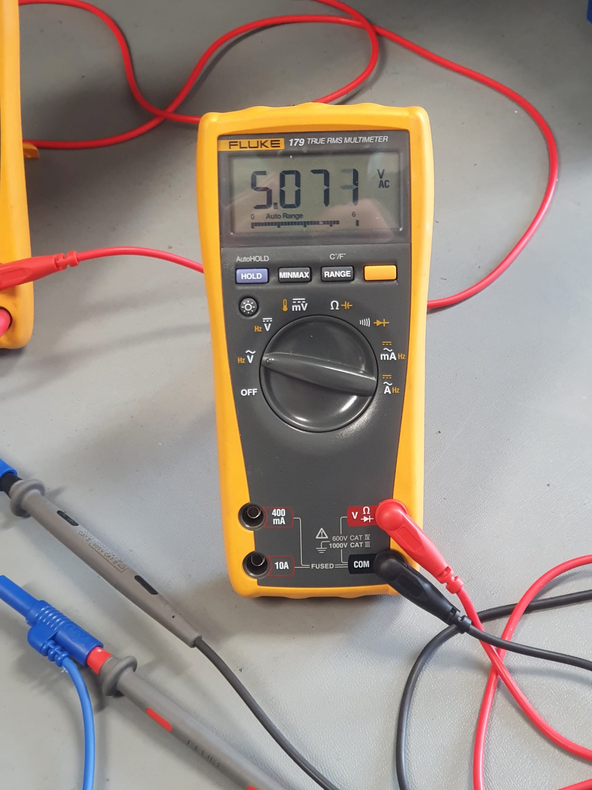
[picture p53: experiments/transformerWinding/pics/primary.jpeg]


### Secondary Voltage
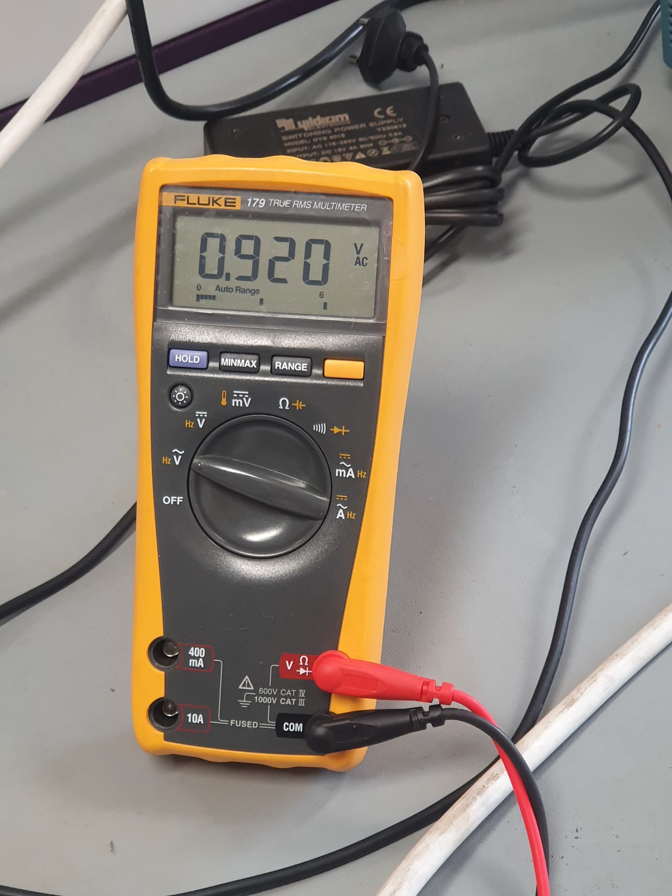
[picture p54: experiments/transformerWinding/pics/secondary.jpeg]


### Primary Current
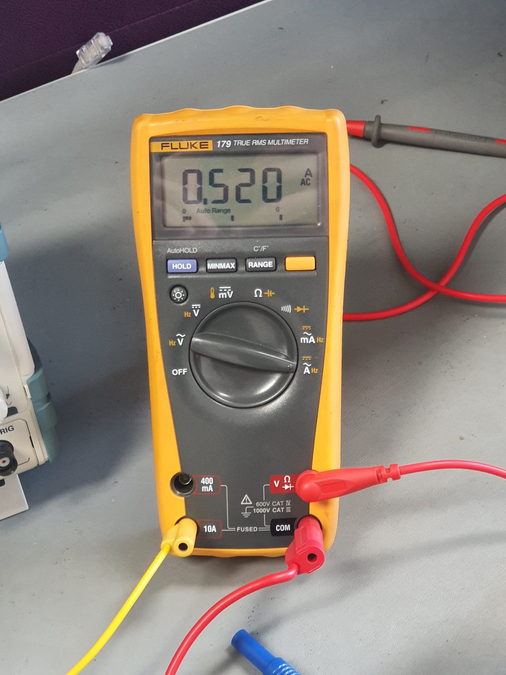
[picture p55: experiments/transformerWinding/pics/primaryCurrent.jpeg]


<center></div>

## Conclusion
&nbsp;&nbsp;&nbsp;&nbsp; DIY transformer winding idea failed. We need to buy a transformer.

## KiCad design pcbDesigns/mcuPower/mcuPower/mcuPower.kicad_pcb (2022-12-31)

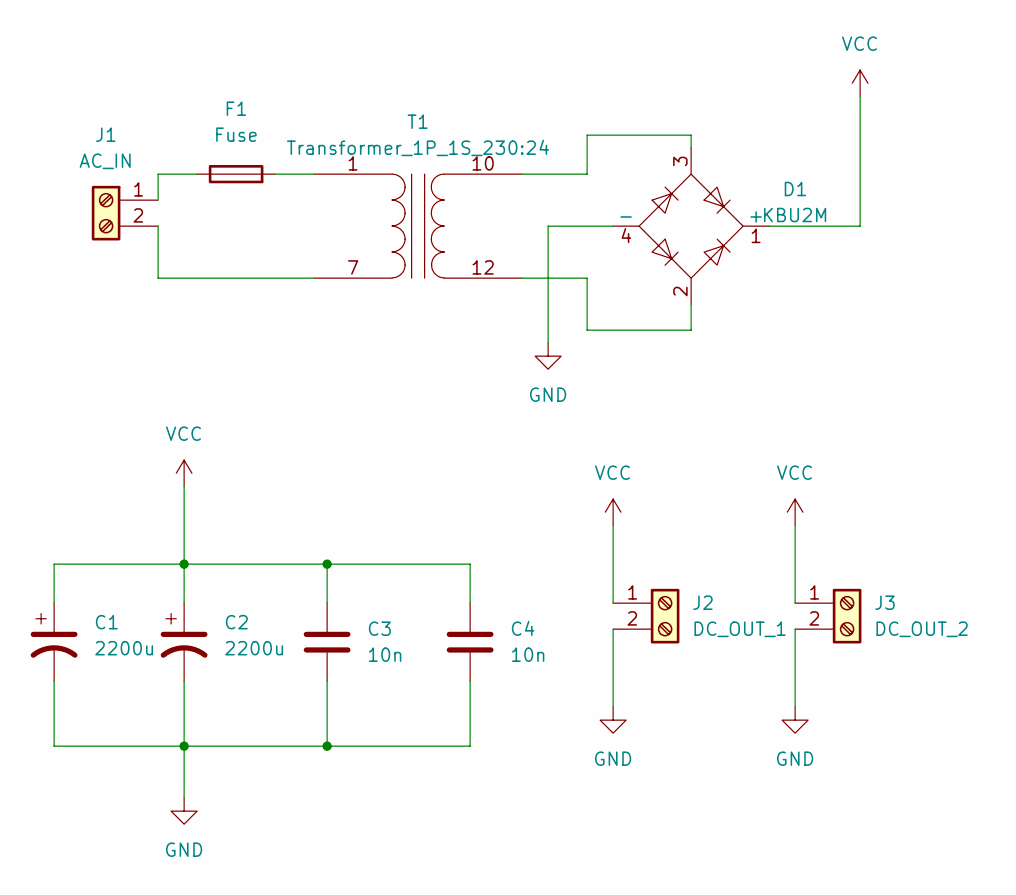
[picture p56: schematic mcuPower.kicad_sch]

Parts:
C1, C2: 2200u; CP_Radial_D16.0mm_P7.50mm
C3, C4: 10n; C_Disc_D5.1mm_W3.2mm_P5.00mm
D1: KBU2M; Diode_Bridge_32.0x5.6x17.0mm_P10.0mm_P7.5mm
F1: Fuse; Fuseholder_Cylinder-5x20mm_Schurter_0031_8201_Horizontal_Op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
J1: AC_IN; TerminalBlock_MetzConnect_Type175_RT02702HBLC_1x02_P7.50mm_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
J2: DC_OUT_1; TerminalBlock_MetzConnect_Type101_RT01602HBWC_1x02_P5.08mm_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
J3: DC_OUT_2; TerminalBlock_MetzConnect_Type101_RT01602HBWC_1x02_P5.08mm_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
T1: Transformer_1P_1S_230:24; Transformer_CHK_EI54-16VA_1xSec

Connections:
GND: C1.2, C2.2, C3.2, C4.2, D1.4 (-), J2.2, J3.2
unnamed: D1.2, T1.12 (SA)
unnamed: D1.3, T1.10 (SB)
unnamed: F1.1, J1.1
unnamed: F1.2, T1.1 (AA)
unnamed: J1.2, T1.7 (AB)
VCC: C1.1, C2.1, C3.1, C4.1, D1.1 (+), J2.1, J3.1

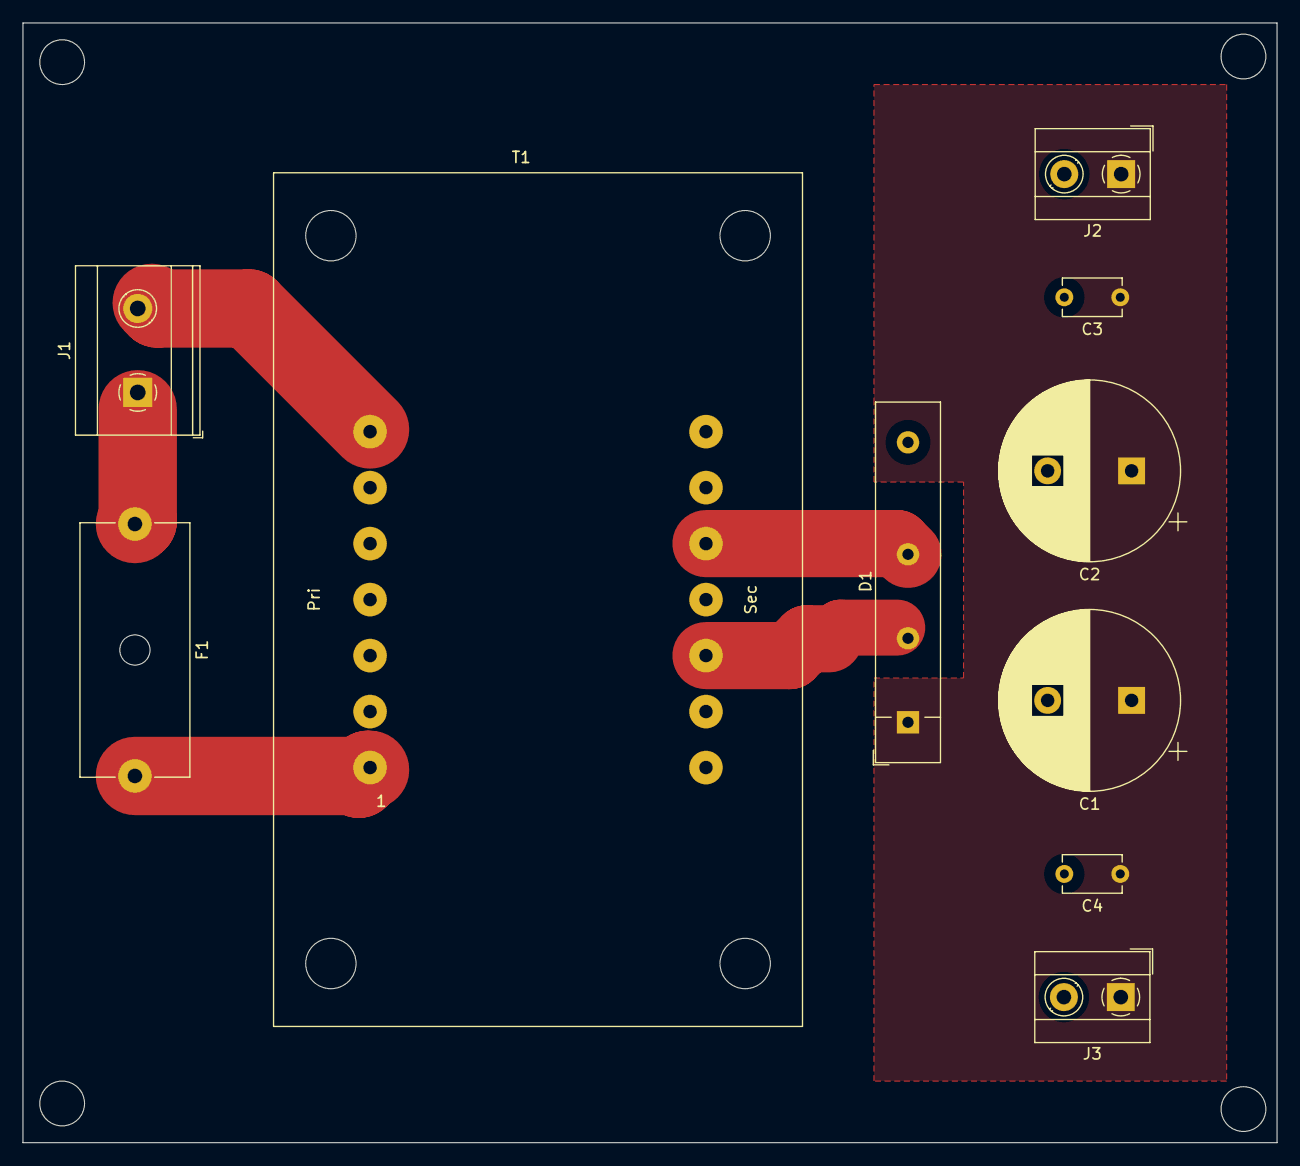
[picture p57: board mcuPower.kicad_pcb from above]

Board: 2 copper layers, 112.0 x 100.0 mm, 10 parts (0 on the bottom side), 7 nets.

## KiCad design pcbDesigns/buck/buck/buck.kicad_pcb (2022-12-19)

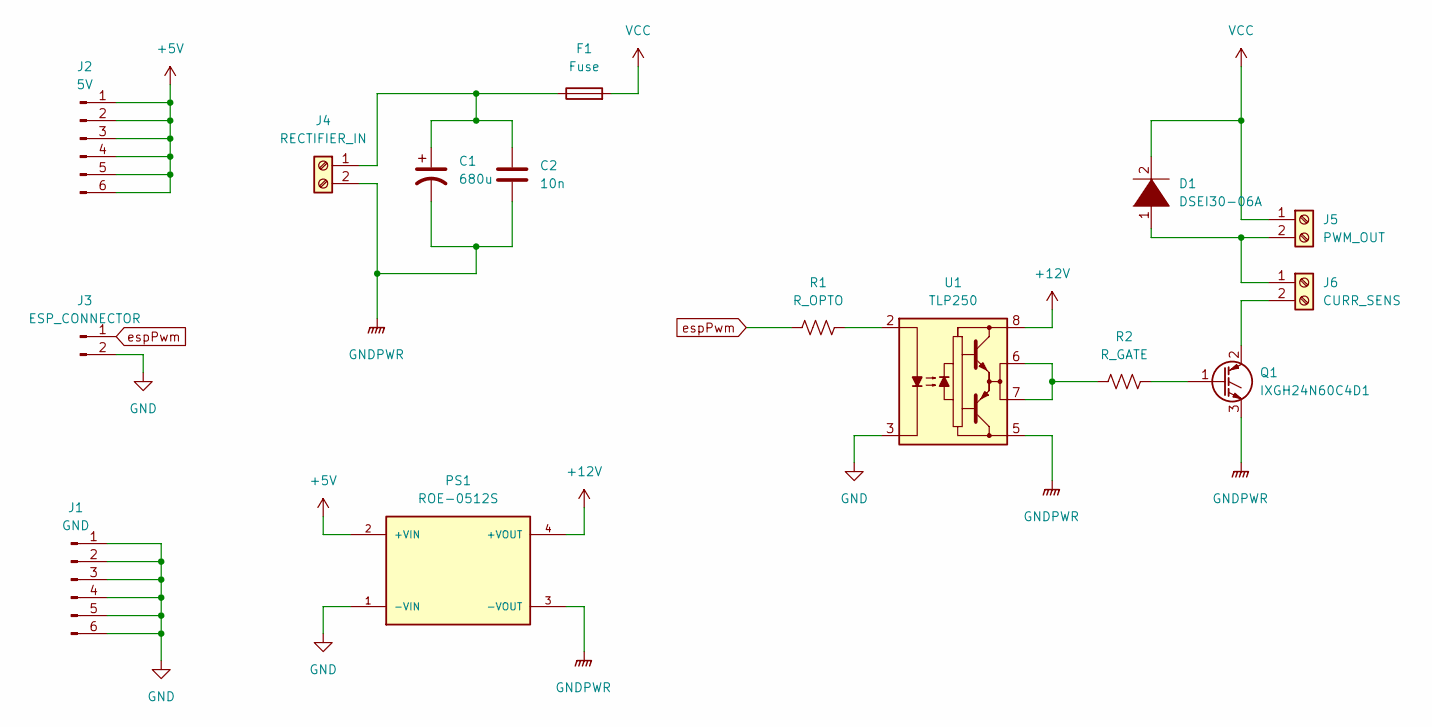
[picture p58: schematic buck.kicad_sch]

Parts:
C1: 680u; CP_Radial_D35.0mm_P10.00mm_SnapIn
C2: 10n; C_Disc_D5.1mm_W3.2mm_P5.00mm
D1: DSEI30-06A; TO-247-2_Vertical
F1: Fuse; Fuseholder_Cylinder-5x20mm_Schurter_0031_8201_Horizontal_Op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
J1: GND; PinHeader_1x06_P2.54mm_Vertical
J2: 5V; PinHeader_1x06_P2.54mm_Vertical
J3: ESP_CONNECTOR; PinHeader_1x02_P2.54mm_Vertical
J4: RECTIFIER_IN; TerminalBlock_MetzConnect_Type175_RT02702HBLC_1x02_P7.50mm_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
J5: PWM_OUT; TerminalBlock_MetzConnect_Type175_RT02702HBLC_1x02_P7.50mm_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
J6: CURR_SENS; TerminalBlock_MetzConnect_Type175_RT02702HBLC_1x02_P7.50mm_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
PS1: ROE-0512S; roe0512; PARTREV 5
Q1: IXGH24N60C4D1; TO-247-3_Vertical
R1: R_OPTO; R_Axial_DIN0204_L3.6mm_D1.6mm_P7.62mm_Horizontal
R2: R_GATE; R_Axial_DIN0204_L3.6mm_D1.6mm_P7.62mm_Horizontal
U1: TLP250; DIP-8_W7.62mm

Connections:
+5V: J2.1, J2.2, J2.3, J2.4, J2.5, J2.6, PS1.2 (+VIN)
+12V: PS1.4 (+VOUT), U1.8 (VCC)
GND: J1.1, J1.2, J1.3, J1.4, J1.5, J1.6, J3.2, PS1.1 (-VIN), U1.3 (C)
GNDPWR: C1.2, C2.2, J4.2, PS1.3 (-VOUT), Q1.3 (E), U1.5 (VEE)
unnamed: C1.1, C2.1, F1.1, J4.1
unnamed: D1.1 (K), J5.2, J6.1
unnamed: J6.2, Q1.2 (C)
unnamed: Q1.1 (G), R2.2
unnamed: R1.2, U1.2 (A)
unnamed: R2.1, U1.6 (VO), U1.7 (VO)
VCC: D1.2 (A), F1.2, J5.1
espPwm: J3.1, R1.1

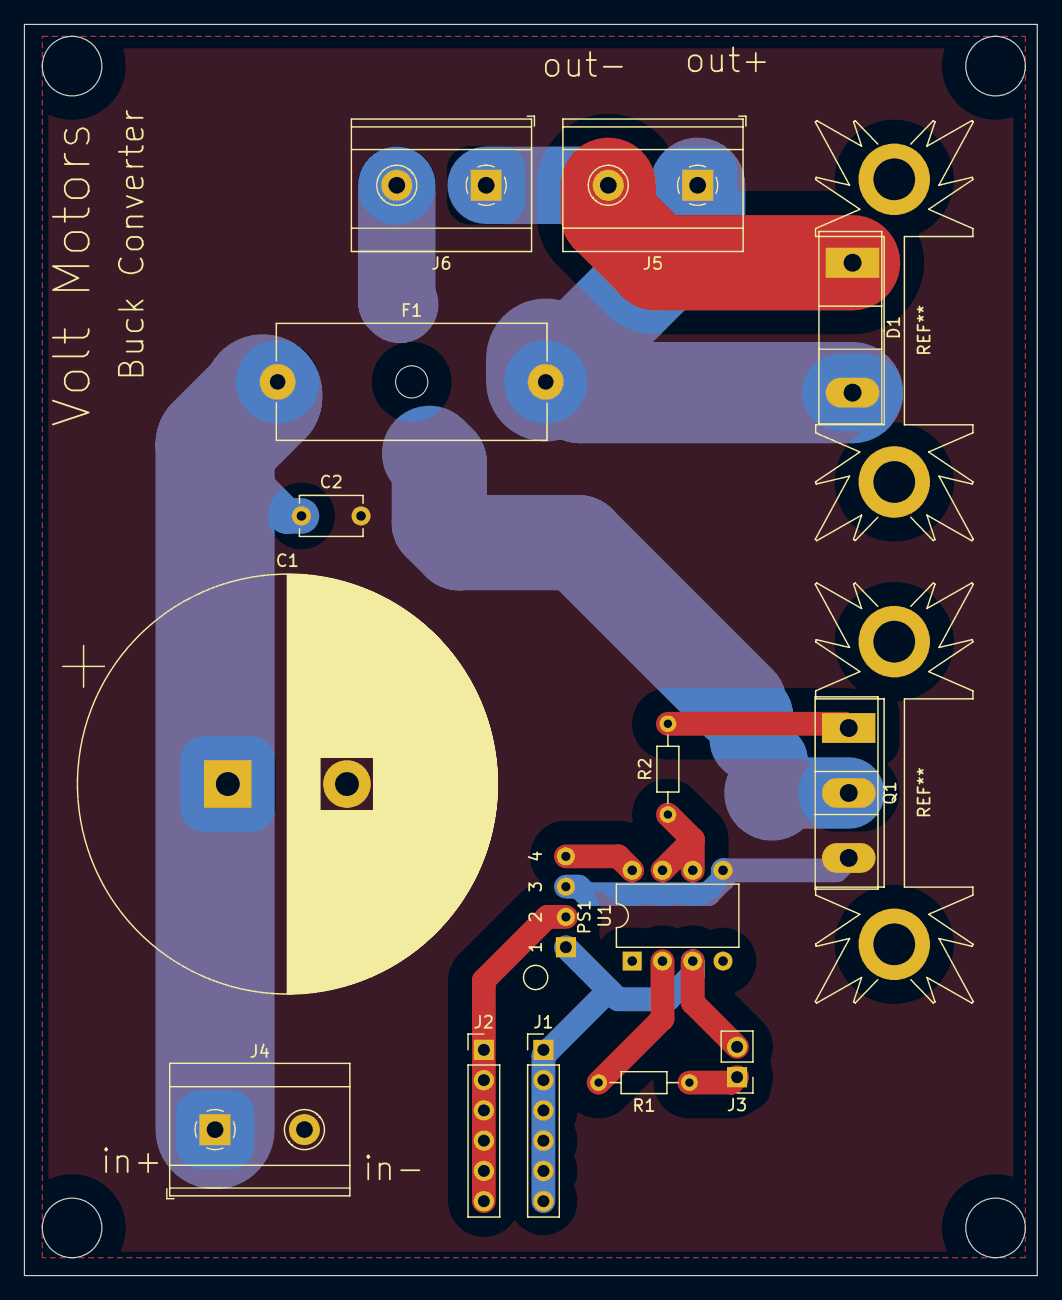
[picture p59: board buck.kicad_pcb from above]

Board: 2 copper layers, 85.0 x 105.0 mm, 15 parts (0 on the bottom side), 12 nets.

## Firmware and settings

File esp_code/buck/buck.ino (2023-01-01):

// https://github.com/Mehmet-Emre-Dogan/smartHome/blob/main/customSonoff/customSonoff.ino
#include <ESP8266WiFi.h>
#include "secrets.h"
#include "pinDefines.h"
#define DEBUG true

//ota
#include <ESP8266mDNS.h>
#include <WiFiUdp.h>
#include <ArduinoOTA.h>

// webWebSerial
#include <ESPAsyncTCP.h>
#include <ESPAsyncWebServer.h>
#include <WebSerial.h>

// CONSTANTS
#define MIN_ALLOWED_PWM 0 //103
#define MAX_ALLOWED_PWM 921
#define MIN_ALLOWED_SPEED 59
#define MAX_ALLOWED_SPEED 1500

#define CURRENT_COEFF 0.0740
#define CURRENT_IGNORE_THRESH 5 // 0-1023
#define CURR_MEAS_SAMPLE_COU 7

const unsigned long accelInterval = 5; // milliseconds

void ICACHE_RAM_ATTR handleBtn();

// GLOBALS
String header; // Variable to store the HTTP request

unsigned long printInterval = 500;
unsigned long lastPrintTime = 0; // milliseconds

const unsigned long analogReadInterval = 50;
unsigned long lastAnalogReadTime = 0; // milliseconds
int prevReadVal = 0;


bool isMachineEnabled = true;
bool isLeft = true;
bool isLeftPrev = true;

int motorPwmTarget = 0;
int motorPwmCurr = 0;
bool isAccelarating = true;
unsigned long lastAccelTime = 0; // milliseconds

float currentCurrent = 20;
float currentSpeed = 0;

int motorSpeedTarget = 0;
int motorSpeedCurr = 0;



// variables for delay without delay() of barrier control

// print server
AsyncWebServer printServer(8080);

void enableInterrupts(){
  attachInterrupt(digitalPinToInterrupt(BTN), handleBtn, CHANGE);
}

void disableInterrupts(){
  detachInterrupt(digitalPinToInterrupt(BTN) );
}

void handleBtn(){
  disableInterrupts();
  delay(10);

  // button mode
  while(!digitalRead(BTN)) // wait until the btn released
    delay(2);
  /*  
  isMachineEnabled = digitalRead(INDICATOR_LED);
  isMachineEnabled = !isMachineEnabled; // toggle current state

  // isMachineEnabled = !digitalRead(BTN); // switch mode, but remote control will cause problems
  digitalWrite(INDICATOR_LED, isMachineEnabled);*/
  
  enableInterrupts();
}

void setup() {
  pinMode(BLUE_LED, OUTPUT);
  pinMode(INDICATOR_LED, OUTPUT);
  pinMode(BTN, INPUT_PULLUP);
  pinMode(CURRENT_SENS_PIN, INPUT);
  digitalWrite(BLUE_LED, LOW);
  digitalWrite(INDICATOR_LED, isMachineEnabled);

  // Connect to Wi-Fi network with SSID and password
  WiFi.disconnect(); 
  WiFi.begin(ssid, password);
  WiFi.hostname(deviceName);
  WiFi.mode(WIFI_STA); //WiFi mode station (connect to wifi router only
  while (WiFi.status() != WL_CONNECTED) {
    digitalWrite(BLUE_LED, LOW);
    delay(400);
    digitalWrite(BLUE_LED, HIGH);                
    delay(100);                            
  }
  WiFi.config(staticIP, subnet, gateway, dns);
  webserver.begin(); // webserver

  // printserver 192.168.1.x:8080/webserial
  WebSerial.begin(&printServer); 
  WebSerial.msgCallback(recvMsg);
  printServer.begin();
  
  /////////////////////////////OTA////////////////////////////
  ArduinoOTA.onStart([]() {
    String type;
    if (ArduinoOTA.getCommand() == U_FLASH) {
      type = "sketch";
    } else { // U_FS
      type = "filesystem";
    }

    // NOTE: if updating FS this would be the place to unmount FS using FS.end()
    //WebSerial.println("Start updating " + type);
  });
  ArduinoOTA.onEnd([]() {
    //WebSerial.println("\nEnd");
  });
  ArduinoOTA.onProgress([](unsigned int progress, unsigned int total) {
    //WebSerial.printf("Progress: %u%%\r", (progress / (total / 100)));
  });
  ArduinoOTA.onError([](ota_error_t error) {
    //WebSerial.printf("Error[%u]: ", error);
    if (error == OTA_AUTH_ERROR) {
      //WebSerial.println("Auth Failed");
      ;
    } else if (error == OTA_BEGIN_ERROR) {
      //WebSerial.println("Begin Failed");
      ;
    } else if (error == OTA_CONNECT_ERROR) {
      //WebSerial.println("Connect Failed");
      ;
    } else if (error == OTA_RECEIVE_ERROR) {
      //WebSerial.println("Receive Failed");
      ;
    } else if (error == OTA_END_ERROR) {
      //WebSerial.println("End Failed");
      ;
    }
  });
  ArduinoOTA.begin();
  ///////////////////////////////////////////////////////////
  
  enableInterrupts();
}

void loop() {
  WiFiClient client = webserver.available();   // Listen for incoming clients

  if (client) {                             // If a new client connects,
    if (DEBUG)  
      WebSerial.println("New Client.");          // print a message out in the WebSerial port
    String currentLine = "";                // make a String to hold incoming data from the client
    while (client.connected()) {            // loop while the client's connected
      if (client.available()) {             // if there's bytes to read from the client,
        char c = client.read();             // read a byte, then
        //if (DEBUG)  
          //Serial.write(c);                    // print it out the WebSerial monitor
        header += c;
        if (c == '\n') {                    // if the byte is a newline character
          // if the current line is blank, you got two newline characters in a row.
          // that's the end of the client HTTP request, so send a response:
          if (currentLine.length() == 0) {
            // HTTP headers always start with a response code (e.g. HTTP/1.1 200 OK)
            // and a content-type so the client knows what's coming, then a blank line:
            client.println("HTTP/1.1 200 OK");
            client.println("Content-type:text/html");
            client.println("Connection: close");
            client.println();
            
            // receive data
            if (header.indexOf("GET /e/run") >= 0){
              isMachineEnabled = 1;
            }
            else if (header.indexOf("GET /e/stop") >= 0){
              isMachineEnabled = 0;
            }
            else if (header.indexOf("GET /sd/?") >= 0) {
                  int index = header.indexOf('?') + 1;
                  String mystr = "";
                  for(; header[index] != '?'; index++){
                    mystr += header[index];
                  }
              int number = mystr.toInt();
              if (number >= MIN_ALLOWED_PWM && number <= MAX_ALLOWED_PWM){
                motorPwmTarget = number; 
                isAccelarating = motorPwmTarget > motorPwmCurr;
              }
            }
            else if (header.indexOf("GET /ss/?") >= 0) {
                  int index = header.indexOf('?') + 1;
                  String mystr = "";
                  for(; header[index] != '?'; index++){
                    mystr += header[index];
                  }
              int number = mystr.toInt();
              if (number >= MIN_ALLOWED_SPEED && number <= MAX_ALLOWED_SPEED){
                motorSpeedTarget = number; 
              }
            }


            if(digitalRead(INDICATOR_LED) != isMachineEnabled){
              digitalWrite(INDICATOR_LED, isMachineEnabled);
           }
            
            // Display the HTML web page
            client.println("<!DOCTYPE html>");
            client.println("<html>");
            client.println("    <head>");
            client.println("<meta http-equiv='content-type' content='text/html; charset=UTF-8'>");
            client.println("<meta charset='utf-8' name='viewport' content='width=device-width, initial-scale=1'>");
            client.println("<style >");
            client.println("html {");
            client.println("  font-family: Helvetica, sans-serif;");
            client.println("  color: white;");
            client.println("  background-color:#333;");
            client.println("  justify-content: center;");
            client.println();
            client.println("}");
            client.println();
            client.println(".container{");
            client.println("  justify-content: center;");
            client.println("  display: flex;");
            client.println("  padding: 20px;");
            client.println("}");
            client.println();
            client.println("h2{");
            client.println("  text-align: center;");
            client.println("  /* font-size: 25px; */");
            client.println("}");
            client.println();
            client.println(".box {");
            client.println("  justify-content: center;");
            client.println("  text-align: justify;");
            client.println("  text-justify: auto;");
            client.println("  font-size: large;");
            client.println("  width: 90%;");
            client.println("  background-color: grey;");
            client.println("  padding: 20px;");
            client.println("  padding-top: 5px;");
            client.println("}");
            client.println();
            client.println("code{");
            client.println("  font-size: x-large;");
            client.println("  text-align: center;");
            client.println("  display: block;");
            client.println("  padding-left: auto;");
            client.println("  padding-right: auto;");
            client.println("}");
            client.println();
            client.println(".codeP{");
            client.println("  background-color: #555;");
            client.println("  width: 85%;");
            client.println("  display: flow-root;");
            client.println("  color: #00FF00;");
            client.println("  padding: 5px;");
            client.println("  border-radius: 3px;");
            client.println("  margin-left: auto;");
            client.println("  margin-right: auto;");
            client.println("}");
            client.println();
            client.println(".btn {");
            client.println("        background-color: DodgerBlue;");
            client.println("        border: none;");
            client.println("        color: white;");
            client.println("        padding: 12px 30px;");
            client.println("        cursor: pointer;");
            client.println("        font-size: 20px;");
            client.println("        margin: auto;");
            client.println("        display: inline-block;");
            client.println("        transition: all 0.2s ease-in-out;");
            client.println("        text-decoration: none;");
            client.println("        }");
            client.println();
            client.println("        /* Darker background on mouse-over */");
            client.println("        .btn:hover {");
            client.println("        background-color: RoyalBlue;");
            client.println("        transition: all 0.2s ease-in-out;");
            client.println("        transform: scale(1.1);");
            client.println("        }");
            client.println();
            client.println(".slidecontainer {");
            client.println("    width: 100%;");
            client.println("  }");
            client.println("  ");
            client.println("  .slider {");
            client.println("    /* -webkit-appearance: none; */");
            client.println("    width: 100%;");
            client.println("    height: 15px;");
            client.println("    border-radius: 5px;");
            client.println("    background: #d3d3d3;");
            client.println("    outline: none;");
            client.println("    opacity: 0.7;");
            client.println("    -webkit-transition: .2s;");
            client.println("    transition: opacity .2s;");
            client.println("  }");
            client.println("  ");
            client.println("  .slider:hover {");
            client.println("    opacity: 1;");
            client.println("  }");
            client.println("  ");
            client.println("  .slider::-webkit-slider-thumb {");
            client.println("    /* -webkit-appearance: none; */");
            client.println("    appearance: none;");
            client.println("    width: 25px;");
            client.println("    height: 25px;");
            client.println("    border-radius: 50%;");
            client.println("    background: #049faa;");
            client.println("    cursor: pointer;");
            client.println("  }");
            client.println("  ");
            client.println("  .slider::-moz-range-thumb {");
            client.println("    width: 25px;");
            client.println("    height: 25px;");
            client.println("    border-radius: 50%;");
            client.println("    background: #07788b;");
            client.println("    cursor: pointer;");
            client.println("  }");
            client.println();
            client.println(".footer {");
            client.println("  left: 0;");
            client.println("  bottom: 0;");
            client.println("  width: 100%;");
            client.println("  background-color: #333;");
            client.println("  color: white;");
            client.println("  text-align: center;");
            client.println("}");
            client.println();
            client.println("/* For desktop: */");
            client.println("@media only screen and (min-width: 800px) {");
            client.println("  html {");
            client.println("    max-width: 60%;");
            client.println("    margin: auto;");
            client.println("  }");
            client.println();
            client.println("  .codeP{");
            client.println("  background-color: #555;");
            client.println("  width: 80%;");
            client.println("  display: flow-root;");
            client.println("  color: #00FF00;");
            client.println("  padding: 5px;");
            client.println("  border-radius: 3px;");
            client.println("  margin-left: auto;");
            client.println("  margin-right: auto;");
            client.println("}");
            client.println(".slidecontainer{");
            client.println("    width: 60%;");
            client.println("    margin: auto;");
            client.println("}");
            client.println("}");
            client.println();
            client.println("  </style>");
            client.println("</head>");
            client.println("<body>");
            client.println("    <h1 style='text-align: center;'>Smart Motor Driver</h1>");
            client.println("    <h3 style='text-align: center;'><a style='text-align: center; color: white; text-decoration: none;' href='https://github.com/Mehmet-Emre-Dogan/EE463_2022_TermProject'>Volt Motors Inc.</a></h3>");
            client.println();
            client.println("        <div class='container'>");
            client.println("            <div class='box'>");
            client.println("                <h2>Stats</h2>");
            client.println();
            client.println("                <div class='slidecontainer'>");
            client.println("                    <code>");
            /*
            client.println("                        <p class='codeP' style='font-size: large;'>");
            client.println("                            Speed [rpm]: --- <br>");
            client.println("                            Duty [/1023]: --- <br>");
            client.println("                            Current [A]: --- <br>");
            client.println("                            Temp [°C]: --- <br>");
            client.println("                            Fan Speed [/1023]: --- <br>");
            client.println("                            ");
            client.println("                        </p>");
            */
            client.println("                        <p class='codeP'>Control Loop: Open<br>");
            client.println("                          Direction: Left ");
            client.println("                        </p>");
            client.println("                        ");
            client.println("                        <a href='/ctrl/toggle'><button class='btn'>Toggle Loop</button></a>");
            client.println("                        <a href='http://192.168.1.80:8080/webserial'><button class='btn'>Open Serial</button></a>");
            client.println("                    <code>");
            client.println("                </div>");
            client.println("            </div>");
            client.println("        </div> ");
            client.println();
            client.println("        <div class='container'>");
            client.println("          <div class='box'>");
            client.println("              <h2>Set Direction</h2>");
            client.println("              <div class='slidecontainer'>");
            client.println("                  <code>");
            client.println("                    <h3 class='codeP' style='color:rgb(253, 98, 98); text-decoration: underline;'>WARNING!</h3>");
            client.println("                      <p class='codeP' style='color:rgb(252, 206, 108);'>Stop before changing direction!<br> ");
            client.println("                        Our company is not responsible for the damages due to user errors.");
            client.println("                      </p>");
            client.println("                      <br>");
            client.println("                      ");
            client.println("                      <a href='/dir/left'><button class='btn'>Left</button></a>");
            client.println("                      <a href='/dir/stop'><button class='btn'>Stop</button></a>");
            client.println("                      <a href='/dir/right'><button class='btn'>Right</button></a>");
            client.println("                  <code>");
            client.println("              </div>");
            client.println("          </div>");
            client.println("      </div> ");
            client.println();
            client.println("        <div class='container'>");
            client.println("            <div class='box'>");
            client.println("                <h2>Open Loop</h2>");
            client.println("                ");
            client.println("                <div class='slidecontainer'>");
            client.println("                    <code>");
            client.println("                        <p class='codeP'>Duty [/1023]: <span id='dutyValue'></span></p>");
            client.println("                        <p class='codeP'>Duty [%]: <span id='dutyPercent'></span></p>");
            client.println("                        <br>");
            client.println("                        <input type='range' min='103' max='921' value='" + String(motorPwmTarget) + "' class='slider' id='dutySlider', oninput='displayDuty()'>");
            client.println("                        <br> <br> <br>");
            client.println("                        <span id='saDuty'>");
            client.println("                            <!-- <a id='aDuty' href='#'><button class='btn'>Set Duty</button></a> -->");
            client.println("                        </span>");
            client.println("                    <code>");
            client.println("                </div>");
            client.println("            </div>");
            client.println("        </div> ");
            client.println();
            client.println("        <div class='container'>");
            client.println("            <div class='box'>");
            client.println("                <h2>Close Loop</h2>");
            client.println();
            client.println("                <div class='slidecontainer'>");
            client.println("                    <code>");
            client.println("                        <p class='codeP'>Speed [rpm]: <span id='speedValue'></span></p>");
            client.println("                        <p class='codeP'>Speed [%]: <span id='speedPercent'></span></p>");
            client.println("                        <br>");
            client.println("                        <input type='range' min='60' max='1500' value='50' class='slider' id='speedSlider', oninput='displaySpeed()'>");
            client.println("                        <br> <br> <br>");
            client.println("                        <span id='saSpeed'>");
            client.println("                            <a id='aSpeed' href='#'><button class='btn'>Set Speed</button></a>");
            client.println("                        </span>");
            client.println("                    <code>");
            client.println("                </div>");
            client.println("            </div>");
            client.println("        </div> ");
            client.println();
            client.println("        <br>");
            client.println("        <br>");
            client.println();
            client.println("        <div class='footer'>© 2022 <br> Web design by medogan <a style='color: #049faa;' href='https://medogan.com'>medogan.com</a></div>");
            client.println("        <br>");
            client.println("        <script>");
            client.println("          function displayDuty(){");
            client.println("            var slider = document.getElementById('dutySlider');");
            client.println("            var dv = document.getElementById('dutyValue');");
            client.println("            var dvpc = document.getElementById('dutyPercent');");
            client.println("            dv.innerHTML = slider.value;");
            client.println("            dvpc.innerHTML = String((Number(slider.value)/1023*100).toFixed(3));");
            client.println();
            client.println("            document.getElementById('saDuty').innerHTML = '<a id=\"aDuty\" href=' + '/sd/?' + slider.value + '?><button class=\"btn\">Set Duty</button></a>';");
            client.println("          }");
            client.println("          function displaySpeed(){");
            client.println("            var slider = document.getElementById('speedSlider');");
            client.println("            var sv = document.getElementById('speedValue');");
            client.println("            var svpc = document.getElementById('speedPercent');");
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

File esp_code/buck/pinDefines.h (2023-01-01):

#ifndef _pinDefines_h_
#define _pinDefines_h_
#define BTN D5
#define INDICATOR_LED D6
#define BLUE_LED LED_BUILTIN
#define MOTOR_PIN D1
#define MOTOR_DIR_PIN D2
#define CURRENT_SENS_PIN A0
#endif

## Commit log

2022-11-22 calculated rated voltage and currents
2022-11-28 create a html webpage
    to later use with esp8266 [the pwm generator]
2022-12-02 tested ESP's pwm
2022-12-02 working on advanced gate driver
2022-12-02 add png versions of bmp images +
    add a current sensor's and some other datasheets
2022-12-02 simulated additional 1 phi low voltage rectifier
2022-12-02 new feature designs
    - single power supply
    - h bridge
    - dynamic braking
2022-12-07 simulation with pwm [mosfet not selected, default used]
2022-12-09 simulated with real diodes and mosfets and
    took screenshots for the report
2022-12-10 Delete Volt Motors-Project Complete Simulation Report.pdf
    The report will be moved in the report folder.
2022-12-10 Simulation v2
    Current measurement block is added to armature winding.
2022-12-11 Update wishlist.md
    add new compnets, change fan cage with correct dimensions
2022-12-11 simulated with 230:24 transformer
    - filtering capacitance doubled (2*2200uF)
    - now using line line instad of line-neutral
2022-12-11 Update wishlist.md
    - ripple with 2200u seemed more to me, so decided to use 2*2200u
    - due to seperation of the fan and control transformers, we need 2 more
2022-12-11 Feedback Presentation of Volt Motors
    Feedback Presentation is completed.
2022-12-11 Version 2
    Another version of the mosfet datasheet is found
2022-12-18 hard coded serial monitor link to the button
2022-12-18 added buck pcb schematic
    [buck.kicad_pcb, buck.kicad_sch]
2022-12-18 designed pcb for the buck
    [buck-B_Cu.gbr, buck-B_Mask.gbr, buck-B_Paste.gbr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]
2022-12-19 revised buck pcb
    revision
    [buck-B_Cu.gbr, buck-B_Mask.gbr, buck-B_Paste.gbr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]
2022-12-19 more revision
    [buck-B_Cu.gbr, buck-B_Mask.gbr, buck-B_Paste.gbr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]
2022-12-19 revision: buck pcb design
    increase clearance
    [buck-B_Cu.gbr, buck-B_Mask.gbr, buck-B_Paste.gbr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]
2022-12-31 designed pcb for the mcu power
    [mcuPower-B_Cu.gbr, mcuPower-B_Mask.gbr, mcuPower-B_Paste.gbr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]
2022-12-31 bugfix
    fix wron connecter direction
    [mcuPower-B_Cu.gbr, mcuPower-B_Mask.gbr, mcuPower-B_Paste.gbr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]
2022-12-31 add pcb pics
2023-01-20 add the deprecated H bridge design
    [ROE-0512S.step, hBridge.kicad_pcb, hBridge.kicad_sch]
2023-01-22 Simulation with Motor Model
2023-01-22 add resistor and correct capacitor values
    [buck.kicad_sch]
2023-01-23 Complete System with 2kW Output Power
2023-01-23 Complete System at Rated Voltage
2023-01-23 Complete System with 2kW Output Power
    Fundamental frequencies of mean block are corrected
2023-01-23 Complete System at Rated Voltage
    Fundamental frequencies of mean blocks are corrected
2023-01-23 Complete System with 2kW Output Power
    Output capacitor is removed due to its ideal characteristic in the simulation and input tork is adjusted
2023-01-23 Complete System at Rated Voltage
    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
2023-01-23 Transformer_Simulation
    Input voltage is corrected
2023-01-24 Complete System with 2kW Output Power
    Waveform measurements are added for armature current and output voltage
2023-01-24 Complete System at Rated Voltage
    Waveform measurements are added for armature current and output voltage. Tork input of motor model is updated.
